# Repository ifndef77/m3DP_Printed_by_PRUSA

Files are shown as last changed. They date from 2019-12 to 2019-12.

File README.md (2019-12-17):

# mini 3D Printer printed by PRUSA i3 MK3

PRUSA i3 MK3를 이용해 프레임을 출력한 mini 3D Printer 입니다.

최대 120mm x 120mm x 120mm 의 출력이 가능합니다.

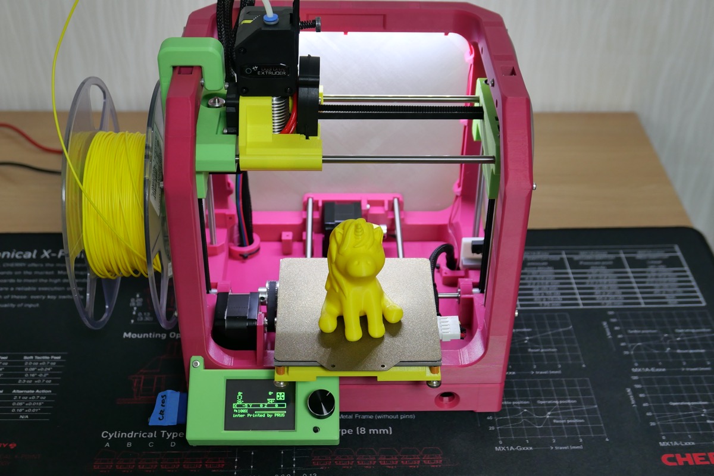
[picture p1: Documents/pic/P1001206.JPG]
P1001206


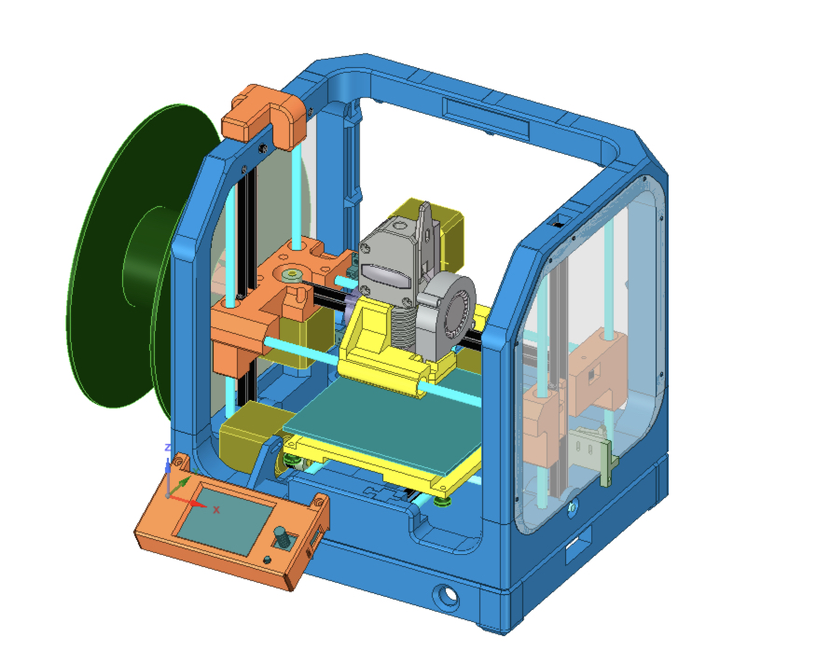
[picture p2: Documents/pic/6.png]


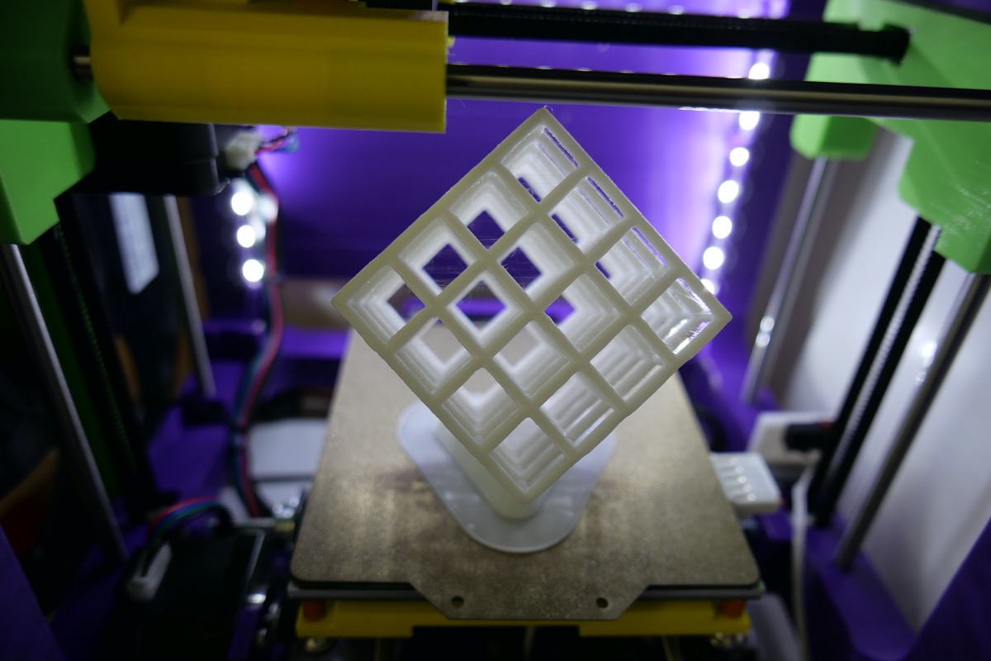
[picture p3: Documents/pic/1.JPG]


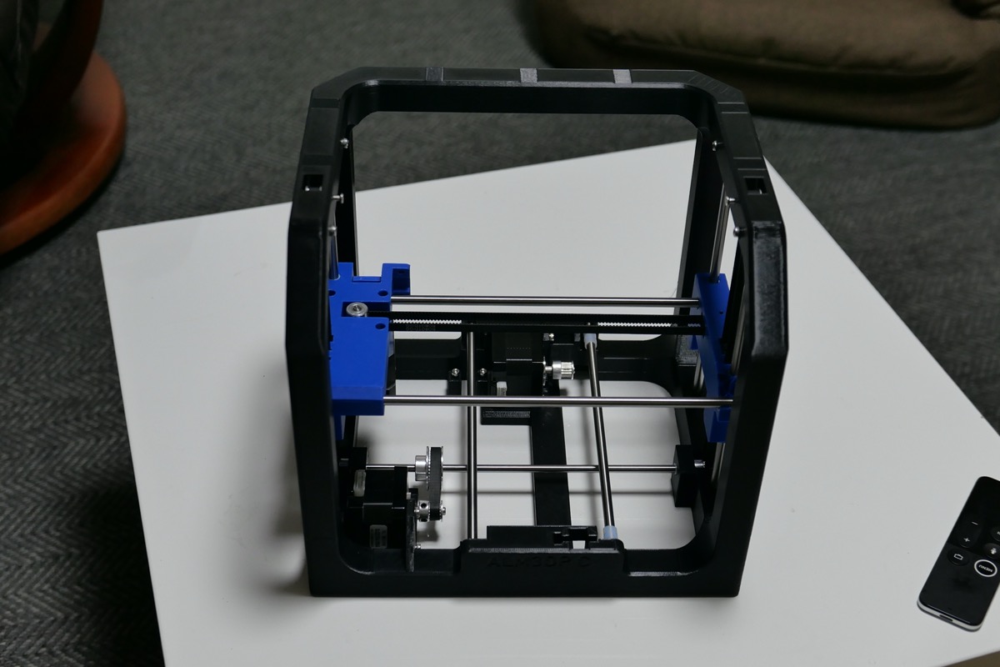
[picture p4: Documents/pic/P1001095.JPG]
P1001095


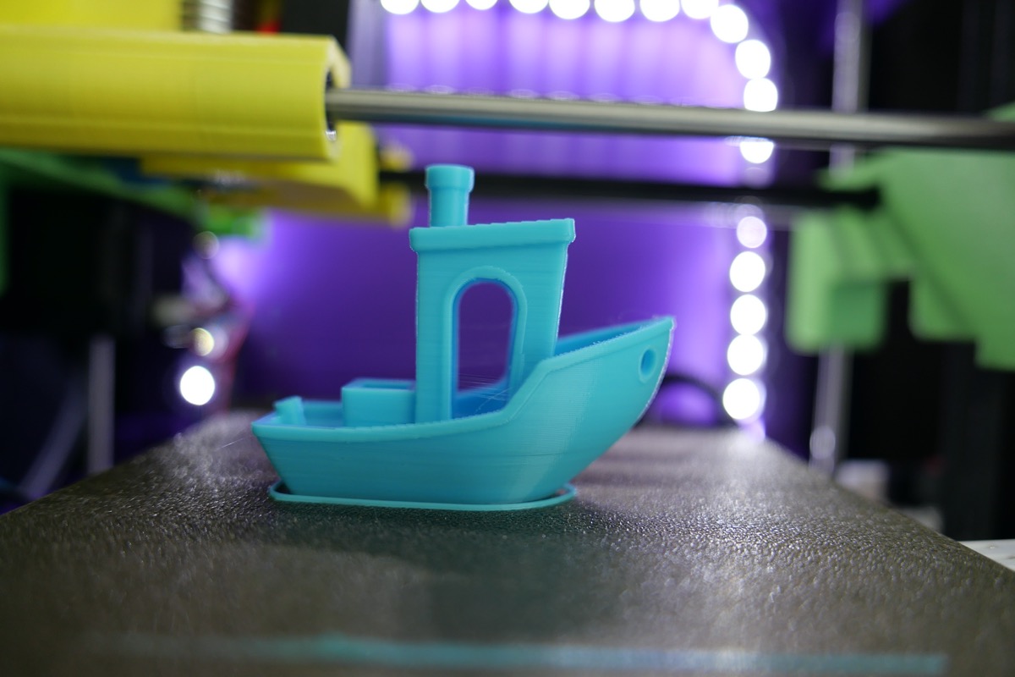
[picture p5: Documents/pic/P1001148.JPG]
P1001148


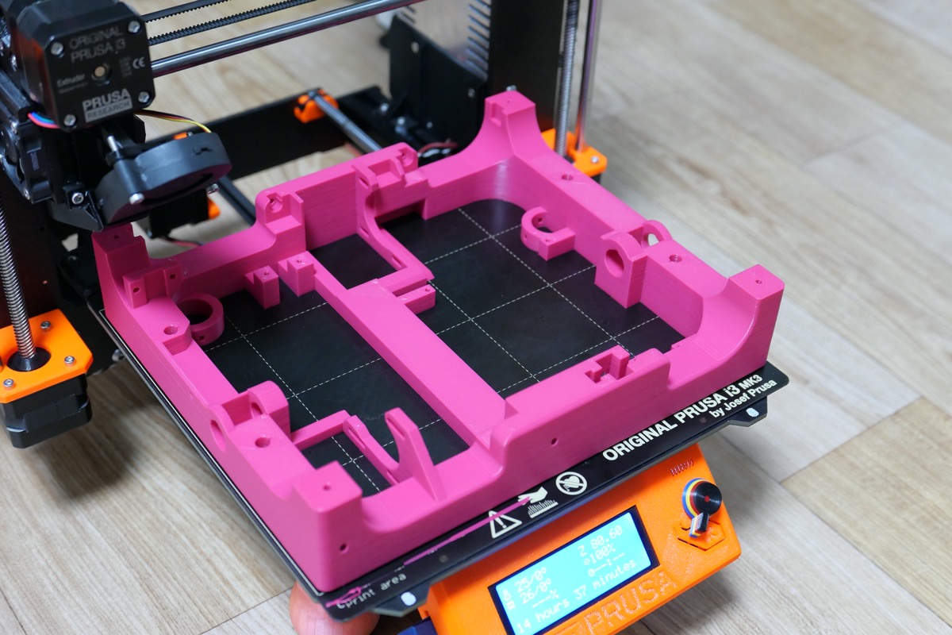
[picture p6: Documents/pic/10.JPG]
P1001155


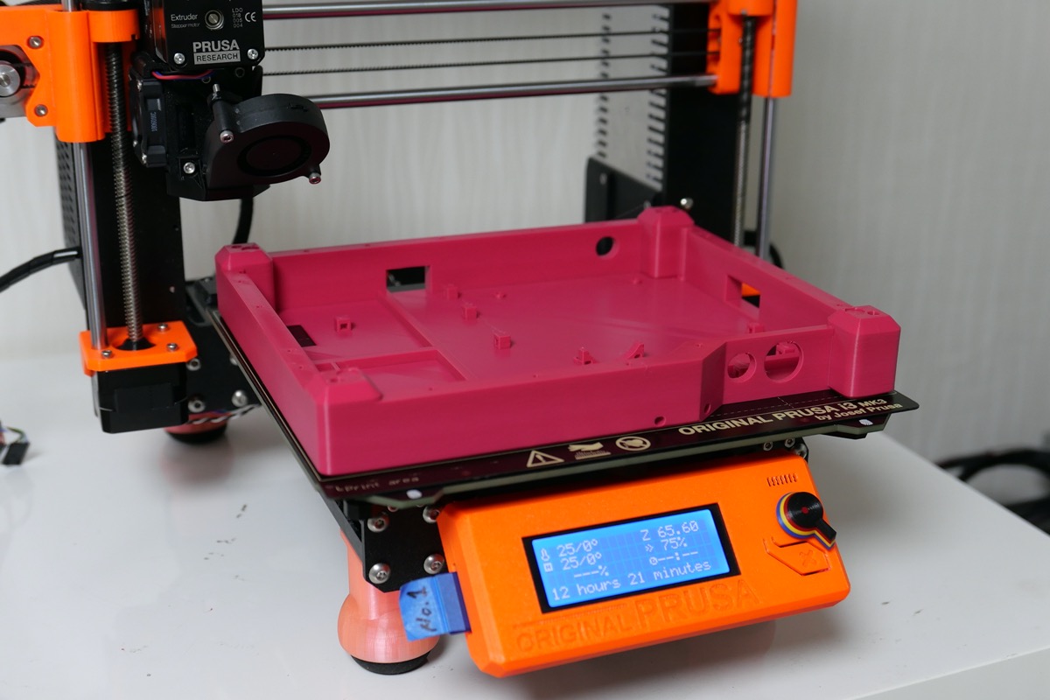
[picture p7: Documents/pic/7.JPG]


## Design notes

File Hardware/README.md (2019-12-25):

## 출력시 주의사항

- 출력물은 모두 PrusaSlicer  높이 0.3mm DRAFT 설정을 사용함
- 바닥면이 큰 출력물의 경우 스커트와 브림설정 없이 출력해야함
- 바닥면이 큰 출력물의 경우 베드온도를 70도로 설정하는것을 권장함
- 노즐덕트, X축 이동부, Y축 베드 지지부는 PETG를 사용해서 출력해야함
- 가급적이면 한대의 프린터를 이용해서 출력하는것을 권장함(공차문제)
- 로드고정방향에 맞추어 x,y축 설정해서 출력하는것을 권장함 (공차문제) - 3MF Files 폴더에 들어있는 3MF파일을 참조



이 저작물은 <a rel="license" href="http://creativecommons.org/licenses/by-sa/4.0/">크리에이티브 커먼즈 저작자표시-동일조건변경허락 4.0 국제 라이선스</a>에 따라 이용할 수 있습니다.

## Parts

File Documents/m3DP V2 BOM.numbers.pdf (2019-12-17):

구동부 부품

No. | 품목 | 단가 | 필요수량 | 비용 | 구매처
1 | 34mm SL 모터 | ₩7,500 | 3 | ₩22,500 | https://smartstore.naver.com/nasspop/products/2462746678
2 | 16t pulley 내경 5mm | ₩500 | 5 | ₩2,500 | https://smartstore.naver.com/nasspop/products/337008823
3 | 16t 아이들러 기어있음 내경 5mm | ₩900 | 4 | ₩3,600 | https://smartstore.naver.com/nasspop/products/554578883
4 | GT2 벨트 | ₩1,300 | 3 | ₩3,900 | https://smartstore.naver.com/nasspop/products/337008935
5 | GT2 loop blet 130mm | US$2.36 | 1 | ₩2,832 | https://ko.aliexpress.com/item/32696696314.html | z축 구동부용
6 | 40t pulley 내경 5mm | US$1.05 | 1 | ₩1,260 | https://ko.aliexpress.com/item/32969569150.html | z축 구동부용
7 | 6mm 연마봉 200mm | ₩3,400 | 2 | ₩3,600 | https://smartstore.naver.com/allbearing/products/403940030 | y축
8 | 6mm 연마봉 220mm | ₩3,740 | 4 | ₩14,960 | https://smartstore.naver.com/allbearing/products/403940030 | z축
9 | 6mm 연마봉 230mm | ₩3,910 | 2 | ₩7,820 | https://smartstore.naver.com/allbearing/products/403940030 | x축
10 | 5mm 연마봉 250mm | ₩5,250 | 1 | ₩5,250 | https://smartstore.naver.com/allbearing/products/403940030 | z축 구동부용
11 | LM6UU 슬라이드 유닛 | ₩600 | 16 | ₩9,600 | https://smartstore.naver.com/nasspop/products/549934645
12 | 605ZZ 베어링 | ₩250 | 4 | ₩1,000 | https://smartstore.naver.com/nasspop/products/554724240

₩78,822

extruder + hotend + bed

No. No. | 품목 | 단가 | 필요수량 | 비용 | 구매처
1 | bmg 익스트루더 | ₩17,900 | 1 | ₩17,900 | https://smartstore.naver.com/nasspop/products/4663607221
2 | 23mm 모터 | ₩6,100 | 1 | ₩6,100 | https://smartstore.naver.com/nasspop/products/2546209750 | 모터만 선택
3 | 30mm 12V 쿨링팬 | ₩3,500 | 1 | ₩3,500 | https://smartstore.naver.com/nasspop/products/449850669

필라멘트

No. | 품목 | 단가 | 필요수량 | 비용 | 구매처
1 | eSUN PLA+ | ₩19,800 | 2 | ₩39,600 | https://smartstore.naver.com/plabs/products/336569947 | 프레임 1롤 기타부분 1롤
2 | 레인보우 PETG | ₩19,800 | 1 | ₩19,800 | https://smartstore.naver.com/cisvision/products/2440785696

₩59,400

₩71,400

No. | 품목 | 단가 | 필요수량 | 비용 | 구매처
4 | 5015 12V 블로워 | ₩1,700 | 1 | ₩1,700 | https://smartstore.naver.com/nasspop/products/4492115644
5 | V6 핫엔드 히트파이프 다이렉트 | ₩1,000 | 1 | ₩1,000 | https://smartstore.naver.com/nasspop/products/2484242557
6 | V6 다이렉트 쓰로트 | ₩500 | 1 | ₩500 | https://smartstore.naver.com/nasspop/products/416327715
7 | V6 신형 히팅 블럭 | ₩1,100 | 1 | ₩1,100 | https://smartstore.naver.com/nasspop/products/2462603952
8 | 0.4mm 노즐 | ₩300 | 1 | ₩300 | https://smartstore.naver.com/nasspop/products/336639199 | 노즐은 가급적 좋은걸로 쓰자
9 | V6 신형 실리콘 커버 | ₩2,600 | 1 | ₩2,600 | https://smartstore.naver.com/nasspop/products/2739366583
10 | 12V 40W 히터 15mm | ₩1,100 | 1 | ₩1,100 | https://smartstore.naver.com/nasspop/products/337008959
11 | 온도센서 | ₩800 | 1 | ₩800 | https://smartstore.naver.com/nasspop/products/2460562958
12 | 120mm x 120mm 12V heat bed | US$11.29 | 1 | ₩13,548 | https://ko.aliexpress.com/item/32822376162.html | 내써팝에서 판매중
13 | 120mm x 120mm pei build plate | US$15.71 | 1 | ₩18,852 | https://ko.aliexpress.com/item/33013575134.html
14 | 베드 스프링 10mm | ₩300 | 4 | ₩1,200 | https://smartstore.naver.com/nasspop/products/3130030215
15 | M3 스텐노브 | ₩300 | 4 | ₩1,200 | https://smartstore.naver.com/nasspop/products/4468280207 | 베드 고정용

제어부

No. | 품목 | 단가 | 필요수량 | 비용 | 구매처
1 | skr 1.3 보드 + tft24 + 2130SPI | US$56.76 | 1 | ₩68,112 | https://www.aliexpress.com/item/4000049709084.html | 신규로 나온 1.4보드 + 2209 추천
2 | optical endstop | US$4.49 | 1 | ₩5,388 | https://www.aliexpress.com/item/32616702945.html | 내써팝에 대체품 있음
3 | 12V 100W 어뎁터 | ₩25,500 | 1 | ₩25,500 | https://smartstore.naver.com/skycplus/products/4136459503
4 | 전원 온오프 스위치 | US$1.00 | 1 | ₩1,200 | https://www.aliexpress.com/item/32922816747.html | 검증못함
5 | LED 스위치 | US$1.39 | 1 | ₩1,668 | https://www.aliexpress.com/item/32996630889.html | 검증못함
6 | DC JACK | US$1.00 | 1 | ₩1,200 | https://www.aliexpress.com/item/32837724336.html | 검증못함
7 | LED STRIP | ₩6,300 | 1 | ₩6,300 | https://smartstore.naver.com/ledbar/products/562352498 | 검증못함
8 | DC-CD LED용 | US$0.75 | 1 | ₩900 | https://ko.aliexpress.com/item/32798886986.html | 검증못함

₩109,368

볼트 & 너트 (정확한 수량 아님 구매시 주의요망)

No. No. | 품목 | 단가 | 필요수량 | 소요비용 | 구매처
1 | 접시머리 M3 18mm | | 2 | | | Z축 아이들 풀리

No. | 품목 | 단가 | 필요수량 | 소요비용 | 구매처
2 | M3 20mm | | 10 | | | X,Y축 아이들 풀리 TOP + BASE 프레임 5015 팬 고정 Z축 벨트 텐셔너
3 | M3 10mm | | 10 | | | BASE + CONTROL BOX LCD 커버 고정 보드 고정
4 | M3 15mm | | 6 | | | 30mm FAN 고정
5 | M3 8mm | | 11 | | | 모터 고정용 파트 쿨링팬 고정
6 | M3 5mm | | | | | 커버고정 로드고정 LCD고정
7 | M3 나일론 너트 | | 2 | | | Z축 벨트 텐셔너
8 | 접시머리 M3 볼트 25mm | | 4 | | | 베드 고정용
9 | M3 38mm 볼트 | | 3 | | | 익스트루더 고정용

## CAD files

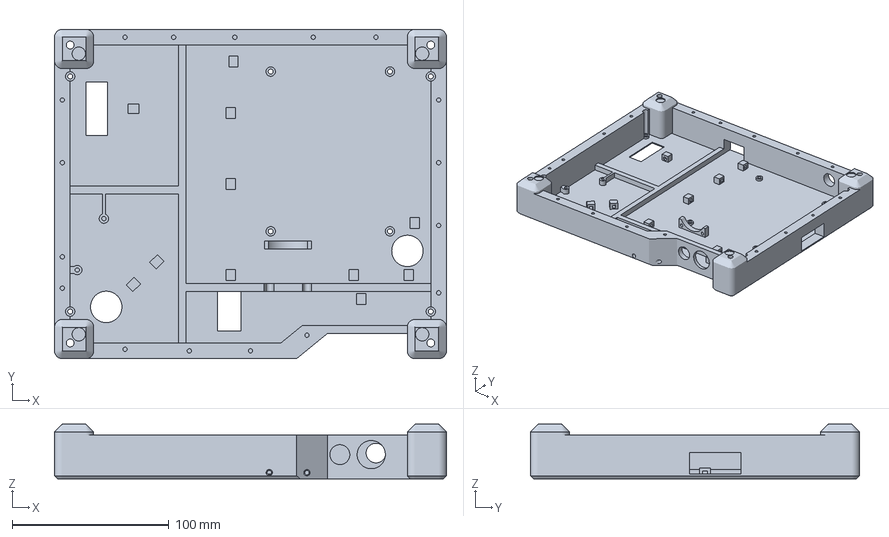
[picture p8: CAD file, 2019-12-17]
Hardware/3MF Files/M3DPC_CONTROLBOX_V2.0.3mf
250.0 x 210.0 x 35.0 mm

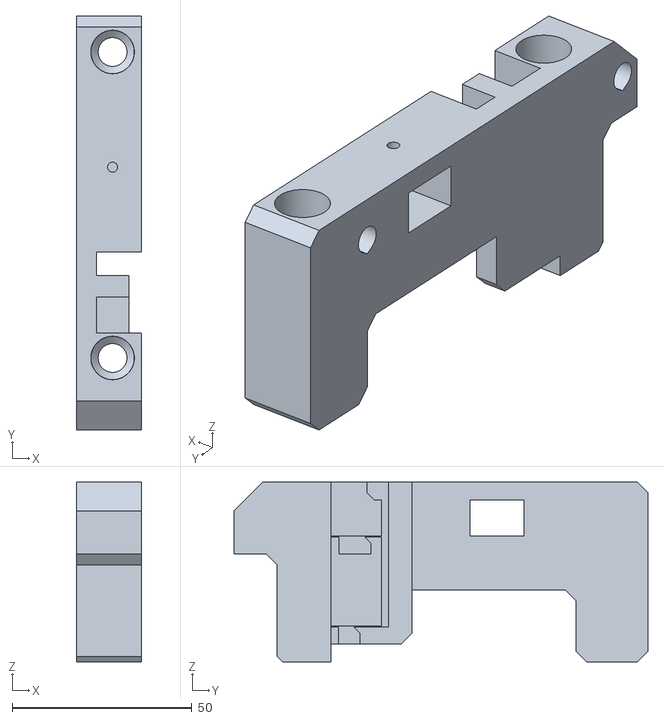
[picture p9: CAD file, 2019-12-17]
Hardware/STL Files/M3DPC_ZRIGHT_V2.1.stl
18.0 x 115.0 x 50.0

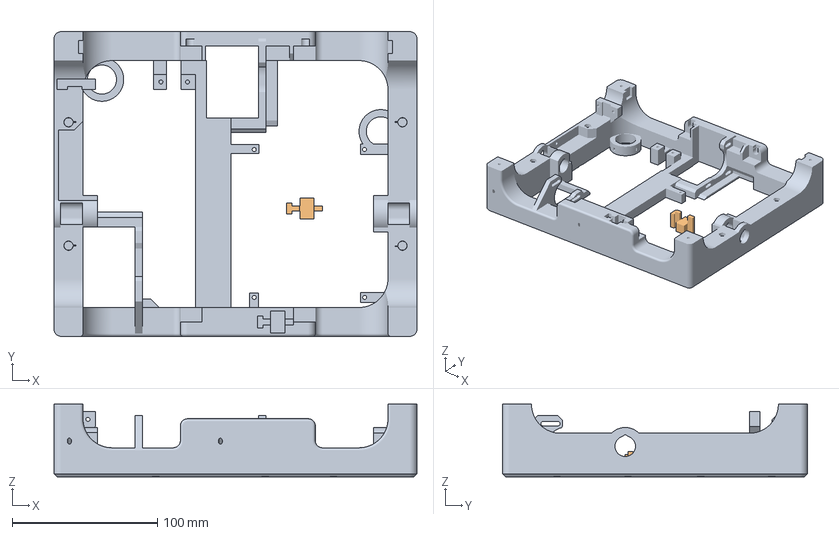
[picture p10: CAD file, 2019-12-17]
Hardware/3MF Files/M3DPC_BASE_V2.3.3mf
250.0 x 209.9 x 50.0 mm
M3DPC_BASE_V2.3.stl
M3DPC_BASE_PULLEYCOVER_V2.0.stl

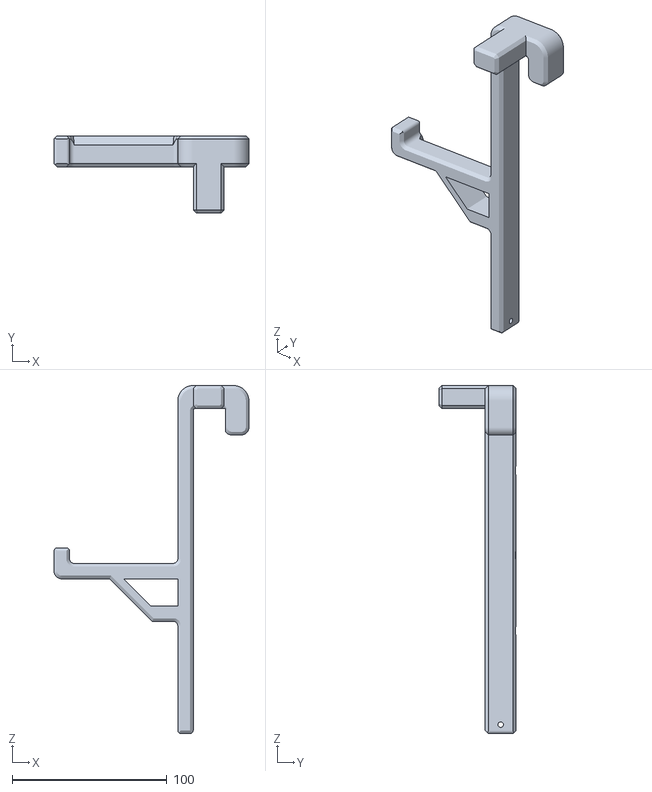
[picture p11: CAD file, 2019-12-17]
Hardware/STL Files/M3DPC_SPOOLHOLDER_V2.2.stl
126.0 x 50.0 x 225.0

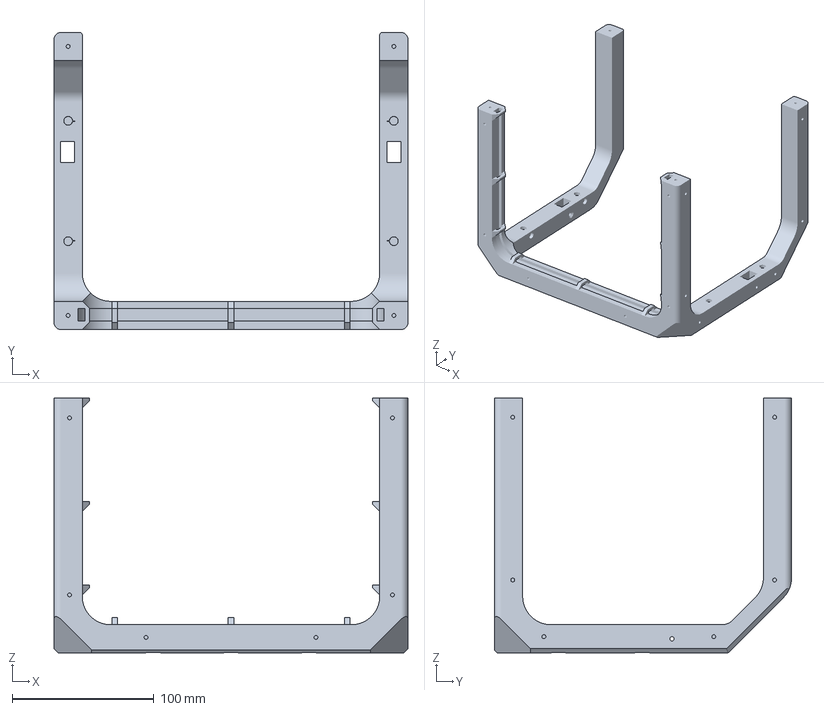
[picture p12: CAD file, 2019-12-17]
Hardware/3MF Files/M3DPC_TOP_V2.2.3mf
250.0 x 209.9 x 179.9 mm

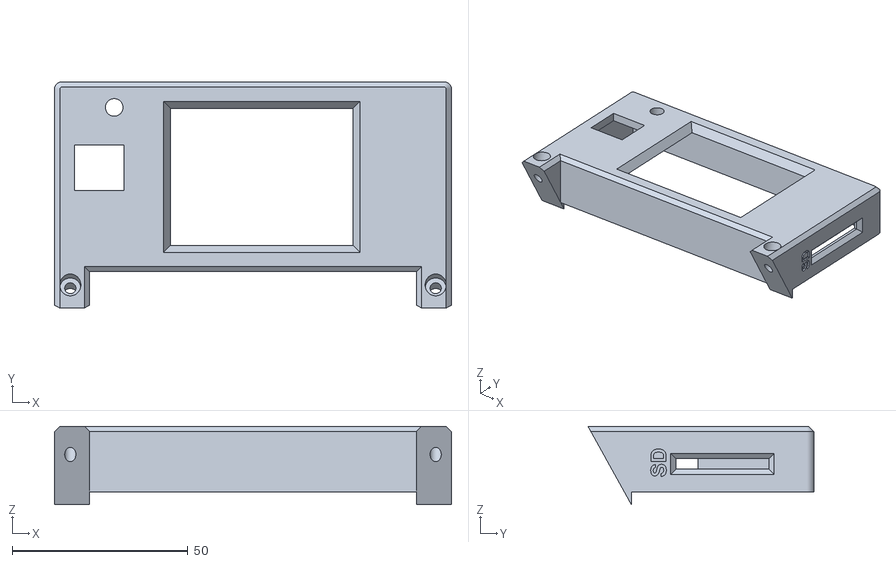
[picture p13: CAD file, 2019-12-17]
Hardware/STL Files/M3DPC_DISPLAY_V2.0.stl
113.0 x 64.4 x 22.3

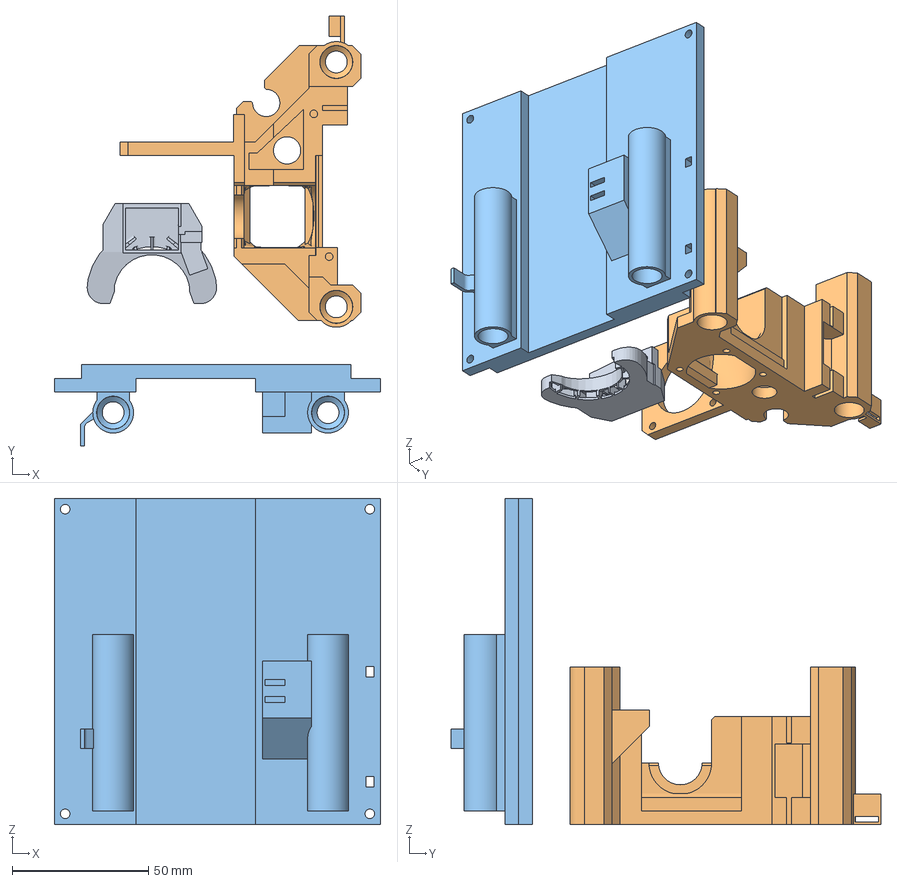
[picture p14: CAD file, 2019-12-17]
Hardware/3MF Files/M3DPC_Y_V2.3.3mf
120.0 x 158.1 x 120.0 mm
M3DPC_XDUCT_V2.2.stl
M3DPC_X_V2.3.stl
M3DPC_Y_V2.3.stl

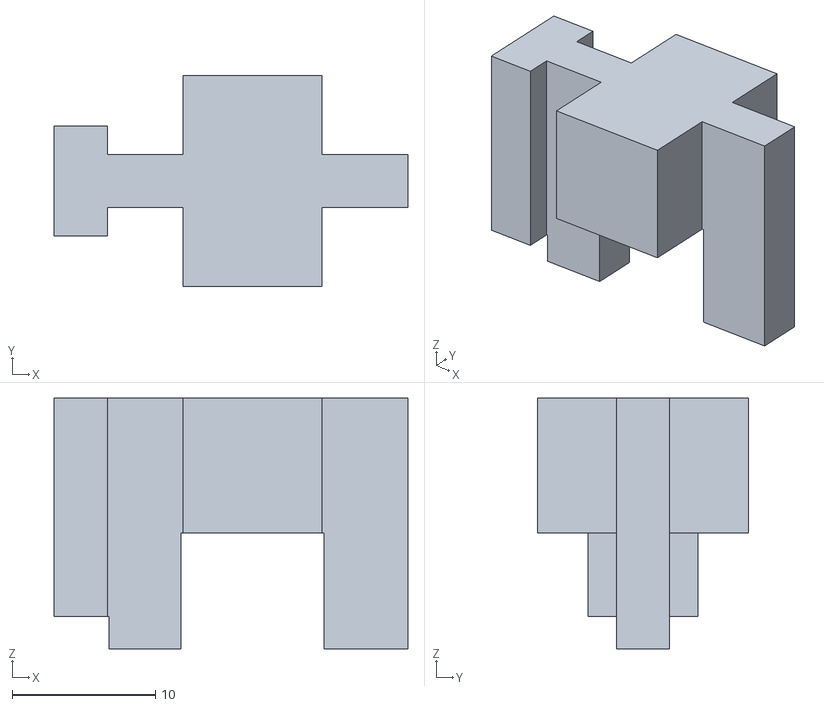
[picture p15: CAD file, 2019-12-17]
Hardware/STL Files/M3DPC_BASE_PULLEYCOVER_V2.0.stl
24.7 x 14.7 x 17.5

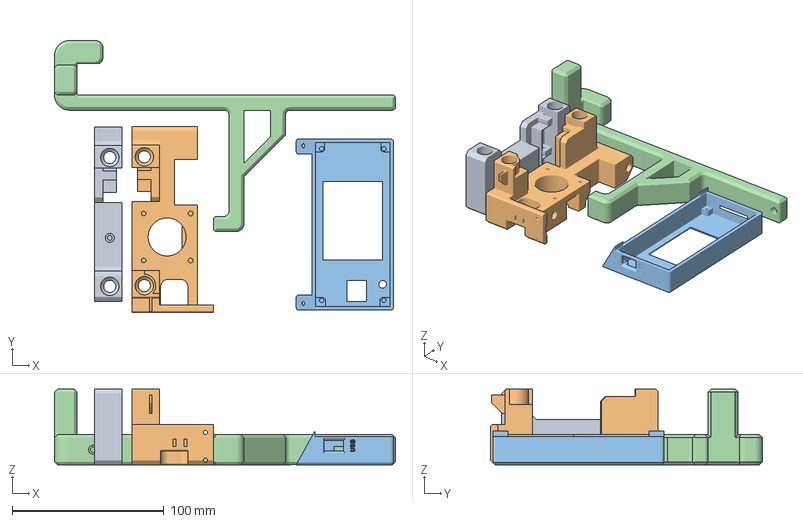
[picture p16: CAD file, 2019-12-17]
Hardware/3MF Files/M3DPC_ZLEFT_V2.3.3mf
225.0 x 179.4 x 50.0 mm
M3DPC_ZRIGHT_V2.1.stl
M3DPC_ZLEFT_V2.3.stl
M3DPC_DISPLAY_V2.0.stl
M3DPC_SPOOLHOLDER_V2.2.stl

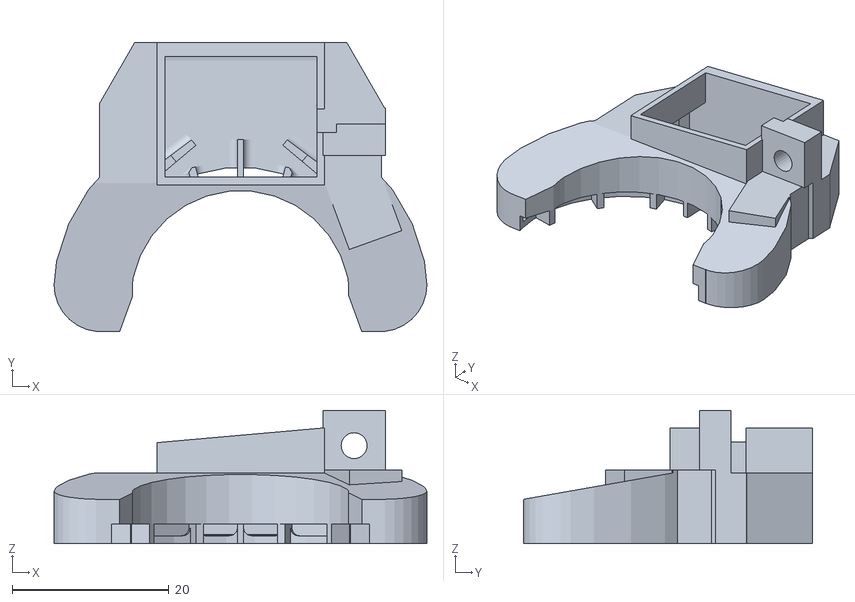
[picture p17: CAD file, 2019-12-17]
Hardware/STL Files/M3DPC_XDUCT_V2.2.stl
47.6 x 36.9 x 17.0

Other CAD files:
Hardware/STL Files/M3DPC_TOP_V2.2.stl
Hardware/STL Files/M3DPC_Y_V2.3.stl
Hardware/STL Files/M3DPC_ZLEFT_V2.3.stl

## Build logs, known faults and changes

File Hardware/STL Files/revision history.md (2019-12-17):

# Revision History

시스템 구성

동작으 위한 최소 공간 : 341mm x 300mm x320mm

---

### TOP

<span style="color:GREEN">**v2.2 :**</span> 191204

- 네임텍 자리 추가
- 외부 커버 장착용 홀 가공
- 아이들어용 볼트 장착부 접시머리용으로 변경

<span style="color:GREEN">**v2.1 :**</span> 191203

- spool holder 고정용 볼팅홀 추가

<span style="color:GREEN">**v2 :**</span> 191130

- 커버제거 - 출력시 면이 길어서 배부름 현상 발생
- ROD 고정부 치수 3.1 → 3.05, 3.2 -> 3.1로 변경
---

### BASE

<span style="color:GREEN">**v2.3 :**</span> 191215

- y축 endstop 간섭으로인한 고정부 위치 변경

<span style="color:GREEN">**v2.2 :**</span> 191204

- 케이블 고정용 기구물 추가
- 컨트롤박스용 고정홀 정리
- 모터 케이블 방향 변경으로 인한 간섭부분 수정

<span style="color:GREEN">**v2.1 :**</span> 191203

- spool holder 고정용 볼팅홀 추가
- 간섭생긴 y endstop 위치변경

<span style="color:GREEN">**v2 :**</span>

- Y 축과 걸리는 부분 위치 수정
- Y 축 endstop 거치부 높이 변경
- Z sync 풀리 고정부 바다면에 R값 추가
- Z sync 605zz 베어링 고정부 수정 14.1mm
- warping 방지용 슬롯 수정
---

### ZLEFT

<span style="color:GREEN">**v2.3 :**</span> 191215

- z축 endstop 간섭부분 수정

<span style="color:GREEN">**v2.2 :**</span> 191204

- 모터 케이블 방향 변경으로 인한 간섭부분 수정
- 브릿지로 지저분하게 보이던 부분 파냄
- endstop trigger 최대로 내림

<span style="color:GREEN">**v2.1 :**</span> 191201

- ROD 고정부 6.0 → 6.1, 6.1 → 6.2

<span style="color:GREEN">**v2 :**</span> 191130

- LM6UU 사용 가능하도록 수정 홀사이즈 : 12.1mm
- ROD 고정부 치수 6.2 -> 6.0, 6.4 -> 6.1로 변경 (티어드롭이 있는 상태임)
- X carriage 30mm fan 간섭부분 잘라냄
- Z sync Pully 고정부 보강 위한 수정
- X endstop 거치부 높이 변경
- 서포트 없이 출력이 가능하도록 30mm fan 간섭부분 형태 변경

---

### ZRIGHT

<span style="color:GREEN">**v2.1 :**</span> 191201

- ROD 고정부 6.0 → 6.1, 6.1 → 6.2

<span style="color:GREEN">**v2 :**</span> 191130

- LM6UU 사용 가능하도록 수정 홀사이즈 : 12.1mm
- ROD 고정부 치수 6.2 -> 6.0, 6.4 -> 6.1로 변경 (티어드롭이 있는 상태임)

---

### Y

<span style="color:GREEN">**v2.3 :**</span> 191215

- 간섭생긴 endstop trigger 위치변경 및 길이 조정

<span style="color:GREEN">**v2.2 :**</span> 191203

- 간섭생긴 endstop trigger 위치변경

<span style="color:GREEN">**v2.1 :**</span> 191202

- 케이블 고정용 케이블 타이홀 작업

<span style="color:GREEN">**v2 :**</span> 191130

- 이름변경 BEDBASE -> Y
- LM6UU 사용 가능하도록 수정 홀사이즈 : 12.1mm
- endstop trigger 높이 수정
- 벨트 수평을 위해 고정부 높이 조절ㅇ
---

### X
<span style="color:GREEN">**v2.3 :**</span> 191215

- endstop trigger 위치 조정

<span style="color:GREEN">**v2.2 :**</span> 191201

- 모터 고정부 오버행용 티어드롭 조정

<span style="color:GREEN">**v2.1 :**</span> 191201

- belt 고정부 간격 2.07 → 1.9로 조정

<span style="color:GREEN">**v2 :**</span> 191130

- LM6UU 사용 가능하도록 수정 홀사이즈 : 12.1mm
- 볼트 머리 닫는 문제 때문에 축 1mm 우측으로 연장
- 핫엔드 고정부 보강
- 모터 익스트루더 조립부 좀더 타이트하게 조정
- 벨트 수평을 위해서 벨트 고정부 위치 조절

---

### X DUCT

<span style="color:GREEN">**v2.2 :**</span> 191210

- 팬 연결부 간섭부분 수정

<span style="color:GREEN">**v2.1 :**</span> 191202

- 히팅블럭 실리콘하고 닿아서 위치 조정

<span style="color:GREEN">**v2.0 :**</span> 191130

- 블로우팬과 간섭 있는 부분 수정
- 한쪽으로만 고정해서 내겨가는 현상 수정위해 X블럭에 닿는 부분 보강

---

### SPOOL HOLDER

<span style="color:GREEN">**v2.2 :**</span> 191204

- 고정부 간격 20mm → 21mm 커버 장착시 고려

<span style="color:GREEN">**v2.1 :**</span> 191203

- 고정용 볼팅홀 추가

<span style="color:GREEN">**v2 :**</span> 191130

- 고정부 폭 21mm → 20mm
- 고정부 길이 추가 연장
- 바닥면 안보이는 면으로 변경
- 스플 무게 중심 고정부 쪽으로 편심되도록 스플 거치부 커팅
- x 모터 축과 간섭 발생하는 부분 수정

----

### CONTROL BOX

<span style="color:GREEN">**v2.0 :**</span> 191204

- 하부 커버 장착 가능하도록 볼팅홀 추가

---

### DISPLAY COVER

<span style="color:GREEN">**v2.0 :**</span> 191204

- 신규작성

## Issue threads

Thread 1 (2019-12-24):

하드웨어 라이선스

edp1096, 2019-12-24:
안녕하세요.
OC카페에서 타고 넘어왔습니다.

좋은 자료 공유해주셔서 감사합니다.

Marlin의 라이선스는 GPL로 알고 있는데,
작업하신 하드웨어 쪽 라이선스도 소프트웨어와 동일하게 GPL인지 아니면 다른 라이선스인지 알고 싶습니다.

ifndef77, 2019-12-25:
하드웨어 관련 라이선스 표기 업데이트 했습니다.

Closed 2019-12-25.

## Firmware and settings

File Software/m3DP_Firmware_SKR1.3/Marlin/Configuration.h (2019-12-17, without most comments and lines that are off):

#pragma once
#define CONFIGURATION_H_VERSION 020000
#define STRING_CONFIG_H_AUTHOR "dotori" // Who made the changes. //+++
#define SHOW_BOOTSCREEN
#define SERIAL_PORT 0
#define SERIAL_PORT_2 -1
#define BAUDRATE 115200
  #define MOTHERBOARD BOARD_BIGTREE_SKR_V1_3
#define CUSTOM_MACHINE_NAME "mini 3D Printer Printed by PRUSA"
#define EXTRUDERS 1
#define DEFAULT_NOMINAL_FILAMENT_DIA 1.75
#define TEMP_SENSOR_0 1
#define TEMP_SENSOR_1 0
#define TEMP_SENSOR_2 0
#define TEMP_SENSOR_3 0
#define TEMP_SENSOR_4 0
#define TEMP_SENSOR_5 0
#define TEMP_SENSOR_BED 1
#define TEMP_SENSOR_CHAMBER 0
#define DUMMY_THERMISTOR_998_VALUE 25
#define DUMMY_THERMISTOR_999_VALUE 100
#define MAX_REDUNDANT_TEMP_SENSOR_DIFF 10
#define TEMP_RESIDENCY_TIME     10  // (seconds) Time to wait for hotend to "settle" in M109
#define TEMP_WINDOW              1  // (°C) Temperature proximity for the "temperature reached" timer
#define TEMP_HYSTERESIS          3  // (°C) Temperature proximity considered "close enough" to the target
#define TEMP_BED_RESIDENCY_TIME 10  // (seconds) Time to wait for bed to "settle" in M190
#define TEMP_BED_WINDOW          1  // (°C) Temperature proximity for the "temperature reached" timer
#define TEMP_BED_HYSTERESIS      3  // (°C) Temperature proximity considered "close enough" to the target
#define HEATER_0_MINTEMP   5 //+++
#define HEATER_1_MINTEMP   5
#define HEATER_2_MINTEMP   5
#define HEATER_3_MINTEMP   5
#define HEATER_4_MINTEMP   5
#define HEATER_5_MINTEMP   5
#define BED_MINTEMP        5 //+++
#define HEATER_0_MAXTEMP 240 //+++
#define HEATER_1_MAXTEMP 275
#define HEATER_2_MAXTEMP 275
#define HEATER_3_MAXTEMP 275
#define HEATER_4_MAXTEMP 275
#define HEATER_5_MAXTEMP 275
#define BED_MAXTEMP      70 //+++
#define PIDTEMP
#define BANG_MAX 255     // Limits current to nozzle while in bang-bang mode; 255=full current //+++++
#define PID_MAX BANG_MAX // Limits current to nozzle while PID is active (see PID_FUNCTIONAL_RANGE below); 255=full current
#define PID_K1 0.95      // Smoothing factor within any PID loop
  #define PID_EDIT_MENU           // Add PID editing to the "Advanced Settings" menu. (~700 bytes of PROGMEM)
  #define PID_AUTOTUNE_MENU       // Add PID auto-tuning to the "Advanced Settings" menu. (~250 bytes of PROGMEM)
  #define PID_FUNCTIONAL_RANGE 10 // If the temperature difference between the target temperature and the actual temperature
  #define DEFAULT_Kp 23.21
  #define DEFAULT_Ki 1.87
  #define DEFAULT_Kd 72.19
#define BED_LIMIT_SWITCHING
#define MAX_BED_POWER 255 // limits duty cycle to bed; 255=full current //+++++
#define PREVENT_COLD_EXTRUSION
#define EXTRUDE_MINTEMP 170
#define PREVENT_LENGTHY_EXTRUDE
#define EXTRUDE_MAXLENGTH 200
#define THERMAL_PROTECTION_HOTENDS // Enable thermal protection for all extruders
#define THERMAL_PROTECTION_BED     // Enable thermal protection for the heated bed
#define THERMAL_PROTECTION_CHAMBER // Enable thermal protection for the heated chamber
#define USE_XMIN_PLUG
#define USE_YMIN_PLUG
#define USE_ZMIN_PLUG
#define ENDSTOPPULLUPS
#define X_MIN_ENDSTOP_INVERTING true // Set to true to invert the logic of the endstop. //+++
#define Y_MIN_ENDSTOP_INVERTING true // Set to true to invert the logic of the endstop. //+++
#define Z_MIN_ENDSTOP_INVERTING false // Set to true to invert the logic of the endstop. //+++
#define X_MAX_ENDSTOP_INVERTING false // Set to true to invert the logic of the endstop.
#define Y_MAX_ENDSTOP_INVERTING false // Set to true to invert the logic of the endstop.
#define Z_MAX_ENDSTOP_INVERTING false // Set to true to invert the logic of the endstop.
#define Z_MIN_PROBE_ENDSTOP_INVERTING false // Set to true to invert the logic of the probe.
#define X_DRIVER_TYPE  TMC2130 //+++
#define Y_DRIVER_TYPE  TMC2130
#define Z_DRIVER_TYPE  TMC2130
#define E0_DRIVER_TYPE TMC2130
#define DEFAULT_AXIS_STEPS_PER_UNIT   { 100, 100, 250, 415 } //+++
#define DEFAULT_MAX_FEEDRATE          { 500, 500, 200, 35 } //+++
#define DEFAULT_MAX_ACCELERATION      { 2000, 2000, 1000, 2000 } //+++
#define DEFAULT_ACCELERATION          1000    // X, Y, Z and E acceleration for printing moves
#define DEFAULT_RETRACT_ACCELERATION  1000   // E acceleration for retracts
#define DEFAULT_TRAVEL_ACCELERATION   1000    // X, Y, Z acceleration for travel (non printing) moves
#define CLASSIC_JERK //+++
  #define DEFAULT_XJERK 10.0
  #define DEFAULT_YJERK 10.0
  #define DEFAULT_ZJERK  0.3
#define DEFAULT_EJERK    5.0  // May be used by Linear Advance
#define S_CURVE_ACCELERATION //+++
#define NOZZLE_TO_PROBE_OFFSET { 10, 10, 0 }
#define MIN_PROBE_EDGE 10
#define XY_PROBE_SPEED 8000
#define Z_PROBE_SPEED_FAST HOMING_FEEDRATE_Z
#define Z_PROBE_SPEED_SLOW (Z_PROBE_SPEED_FAST / 2)
#define Z_CLEARANCE_DEPLOY_PROBE   10 // Z Clearance for Deploy/Stow
#define Z_CLEARANCE_BETWEEN_PROBES  5 // Z Clearance between probe points
#define Z_CLEARANCE_MULTI_PROBE     5 // Z Clearance between multiple probes
#define Z_PROBE_LOW_POINT          -2 // Farthest distance below the trigger-point to go before stopping
#define Z_PROBE_OFFSET_RANGE_MIN -20
#define Z_PROBE_OFFSET_RANGE_MAX 20
#define X_ENABLE_ON 0
#define Y_ENABLE_ON 0
#define Z_ENABLE_ON 0
#define E_ENABLE_ON 0 // For all extruders
#define DISABLE_X false
#define DISABLE_Y false
#define DISABLE_Z false
#define DISABLE_E false             // For all extruders
#define INVERT_X_DIR true
#define INVERT_Y_DIR true
#define INVERT_Z_DIR true
#define INVERT_E0_DIR true
#define INVERT_E1_DIR false
#define INVERT_E2_DIR false
#define INVERT_E3_DIR false
#define INVERT_E4_DIR false
#define INVERT_E5_DIR false
#define X_HOME_DIR -1
#define Y_HOME_DIR -1
#define Z_HOME_DIR -1
#define X_BED_SIZE 120 //+++
#define Y_BED_SIZE 120
#define X_MIN_POS -4 //+++
#define Y_MIN_POS -5 //+++
#define Z_MIN_POS 0 //++++
#define X_MAX_POS X_BED_SIZE
#define Y_MAX_POS Y_BED_SIZE
#define Z_MAX_POS 120
#define MIN_SOFTWARE_ENDSTOPS
  #define MIN_SOFTWARE_ENDSTOP_X
  #define MIN_SOFTWARE_ENDSTOP_Y
  #define MIN_SOFTWARE_ENDSTOP_Z
#define MAX_SOFTWARE_ENDSTOPS
  #define MAX_SOFTWARE_ENDSTOP_X
  #define MAX_SOFTWARE_ENDSTOP_Y
  #define MAX_SOFTWARE_ENDSTOP_Z
  #define SOFT_ENDSTOPS_MENU_ITEM  // Enable/Disable software endstops from the LCD
#define LEVEL_BED_CORNERS
  #define LEVEL_CORNERS_INSET 5    // (mm) An inset for corner leveling
  #define LEVEL_CORNERS_Z_HOP  4.0  // (mm) Move nozzle up before moving between corners
  #define LEVEL_CORNERS_HEIGHT 0.0  // (mm) Z height of nozzle at leveling points
  #define LEVEL_CENTER_TOO        // Move to the center after the last corner
#define HOMING_FEEDRATE_XY (50*60) //++++
#define HOMING_FEEDRATE_Z  (20*60) //+++
#define VALIDATE_HOMING_ENDSTOPS
#define EEPROM_SETTINGS       // Persistent storage with M500 and M501
#define EEPROM_CHITCHAT       // Give feedback on EEPROM commands. Disable to save PROGMEM.
#define HOST_KEEPALIVE_FEATURE        // Disable this if your host doesn't like keepalive messages
#define DEFAULT_KEEPALIVE_INTERVAL 2  // Number of seconds between "busy" messages. Set with M113.
#define BUSY_WHILE_HEATING            // Some hosts require "busy" messages even during heating
#define PREHEAT_1_LABEL       "PLA"
#define PREHEAT_1_TEMP_HOTEND 215
#define PREHEAT_1_TEMP_BED     55
#define PREHEAT_1_FAN_SPEED   0 // Value from 0 to 255
#define PREHEAT_2_LABEL       "ABS"
#define PREHEAT_2_TEMP_HOTEND 240
#define PREHEAT_2_TEMP_BED      0
#define PREHEAT_2_FAN_SPEED   0 // Value from 0 to 255
#define NOZZLE_PARK_FEATURE //+++
  #define NOZZLE_PARK_POINT { (X_MAX_POS/2), (Y_MIN_POS +2), 20 }
  #define NOZZLE_PARK_XY_FEEDRATE 100   // (mm/s) X and Y axes feedrate (also used for delta Z axis)
  #define NOZZLE_PARK_Z_FEEDRATE 10      // (mm/s) Z axis feedrate (not used for delta printers)
#define PRINTJOB_TIMER_AUTOSTART
#define LCD_LANGUAGE en
#define DISPLAY_CHARSET_HD44780 WESTERN
#define SDSUPPORT
#define REVERSE_SELECT_DIRECTION //+++
#define INDIVIDUAL_AXIS_HOMING_MENU
#define SPEAKER
#define LCD_FEEDBACK_FREQUENCY_DURATION_MS 20
#define LCD_FEEDBACK_FREQUENCY_HZ 1000
#define REPRAP_DISCOUNT_FULL_GRAPHIC_SMART_CONTROLLER //+++
#define SOFT_PWM_SCALE 0
#define SERVO_DELAY { 300 }

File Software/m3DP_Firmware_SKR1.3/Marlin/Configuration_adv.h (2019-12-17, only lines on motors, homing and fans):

#define E0_AUTO_FAN_PIN FAN1_PIN //+++
#define E1_AUTO_FAN_PIN -1
#define E2_AUTO_FAN_PIN -1
#define E3_AUTO_FAN_PIN -1
#define E4_AUTO_FAN_PIN -1
#define E5_AUTO_FAN_PIN -1
#define CHAMBER_AUTO_FAN_PIN -1
#define X_HOME_BUMP_MM 0 //+++
#define Y_HOME_BUMP_MM 0
#define Z_HOME_BUMP_MM 2
#define HOMING_BUMP_DIVISOR { 2, 2, 8}  // Re-Bump Speed Divisor (Divides the Homing Feedrate)
#define HOMING_BACKOFF_MM { 0, 0, 5 }  // (mm) Move away from the endstops after homing
#define MICROSTEP_MODES { 16, 16, 16, 16, 16, 16 } // [1,2,4,8,16]
#define DIGIPOT_I2C_MOTOR_CURRENTS { 1.0, 1.0, 1.0, 1.0, 1.0, 1.0, 1.0, 1.0 }  //  AZTEEG_X3_PRO
#define LIN_ADVANCE //+++
  #define LIN_ADVANCE_K 0.08     // Unit: mm compression per 1mm/s extruder speed
#define ADVANCED_PAUSE_FEATURE //+++
  #define ADVANCED_PAUSE_PURGE_FEEDRATE       5  // (mm/s) Extrude feedrate (after loading). Should be slower than load feedrate.
  #define ADVANCED_PAUSE_PURGE_LENGTH         20  // (mm) Length to extrude after loading.
  #define ADVANCED_PAUSE_RESUME_PRIME          0  // (mm) Extra distance to prime nozzle after returning from park.
  #define ADVANCED_PAUSE_FANS_PAUSE               // Turn off print-cooling fans while the machine is paused.
    #define X_CURRENT       700        // (mA) RMS current. Multiply by 1.414 for peak current.
    #define X_CURRENT_HOME  X_CURRENT  // (mA) RMS current for sensorless homing
    #define X_MICROSTEPS     16     // 0..256
    #define Y_CURRENT       700
    #define Y_CURRENT_HOME  Y_CURRENT
    #define Y_MICROSTEPS     16
    #define Z_CURRENT       1000
    #define Z_CURRENT_HOME  Z_CURRENT
    #define Z_MICROSTEPS     16
    #define E0_CURRENT      500
    #define E0_MICROSTEPS    16
    #define CURRENT_STEP_DOWN     50  // [mA]
    #define REPORT_CURRENT_CHANGE
  #define X_HYBRID_THRESHOLD     100  // [mm/s]
  #define X2_HYBRID_THRESHOLD    100
  #define Y_HYBRID_THRESHOLD     100
  #define Y2_HYBRID_THRESHOLD    100
  #define Z_HYBRID_THRESHOLD       3
  #define Z2_HYBRID_THRESHOLD      3
  #define Z3_HYBRID_THRESHOLD      3
  #define E0_HYBRID_THRESHOLD     30
  #define E1_HYBRID_THRESHOLD     30
  #define E2_HYBRID_THRESHOLD     30
  #define E3_HYBRID_THRESHOLD     30
  #define E4_HYBRID_THRESHOLD     30
  #define E5_HYBRID_THRESHOLD     30
  #define SENSORLESS_HOMING // StallGuard capable drivers only //++++
    #define X_STALL_SENSITIVITY  8 //+++
    #define Y_STALL_SENSITIVITY  8 //+++
    #define HOME_USING_SPREADCYCLE //+++
    #define IMPROVE_HOMING_RELIABILITY //+++

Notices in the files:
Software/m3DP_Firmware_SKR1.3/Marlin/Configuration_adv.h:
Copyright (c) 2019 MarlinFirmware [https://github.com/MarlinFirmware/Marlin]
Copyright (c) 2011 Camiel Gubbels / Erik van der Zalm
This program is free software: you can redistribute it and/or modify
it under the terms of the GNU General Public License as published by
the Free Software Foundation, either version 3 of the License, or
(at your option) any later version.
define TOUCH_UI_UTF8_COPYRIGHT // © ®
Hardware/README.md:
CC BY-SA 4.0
